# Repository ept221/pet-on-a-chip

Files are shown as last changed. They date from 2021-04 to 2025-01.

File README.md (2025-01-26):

# Pet On A Chip
Pet on a chip is a project which condenses the control logic the robot described in Frank DaCosta's book "How to Build Your Own Working Robot Pet" onto a single FPGA. More details, pictures, and videos can be found on this [blog post](https://ezrasrobots.wordpress.com/2021/07/07/pet-on-a-chip/).

## tinySoC
tinySoC is a small system on a chip responsible for controlling the robot. It consists of an 8-bit CPU, an 80 column VGA graphics controller, a programmable interrupt controller, GPIO, counter/timer peripherals, dual closed loop motor controllers, a servo controller, a sonar controller, and a UART, all implemented on an iCE40 FPGA. It also comes with an assembler and utilities for loading programs into the chip's internal block memory without having to rerun synthesis and place-and-route.

## The CPU
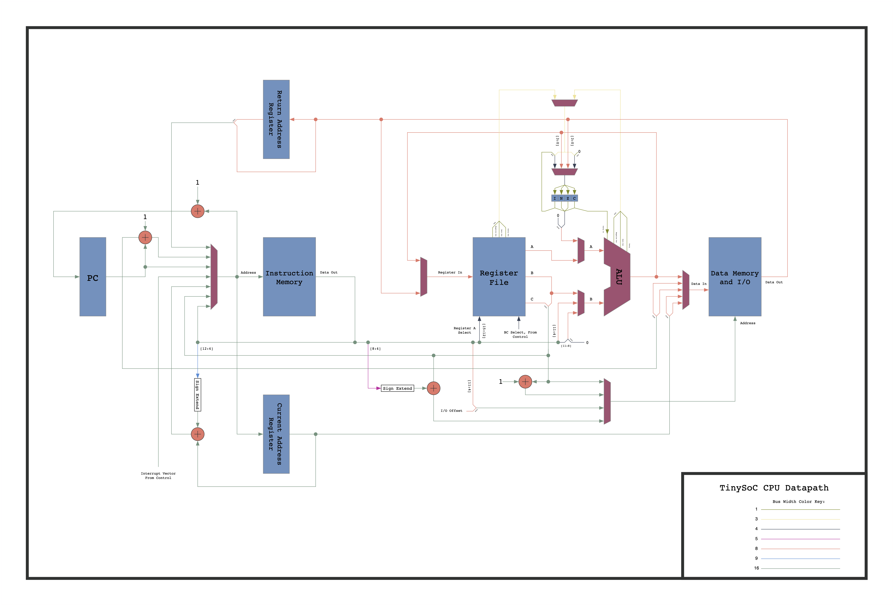
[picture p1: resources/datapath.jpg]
datapath

The CPU is an 8-bit RISC core, with a Harvard architecture. It has a 16-bit wide instruction memory, an 8-bit wide data memory, and both have a 16-bit address. The CPU has 16 general purpose 8-bit registers along with a 4-bit status register. The processor is not fully pipelined, but does fetch the next instruction while executing the current one. Most instructions execute in a single clock cycle, but a few take two or three.

## The GPU
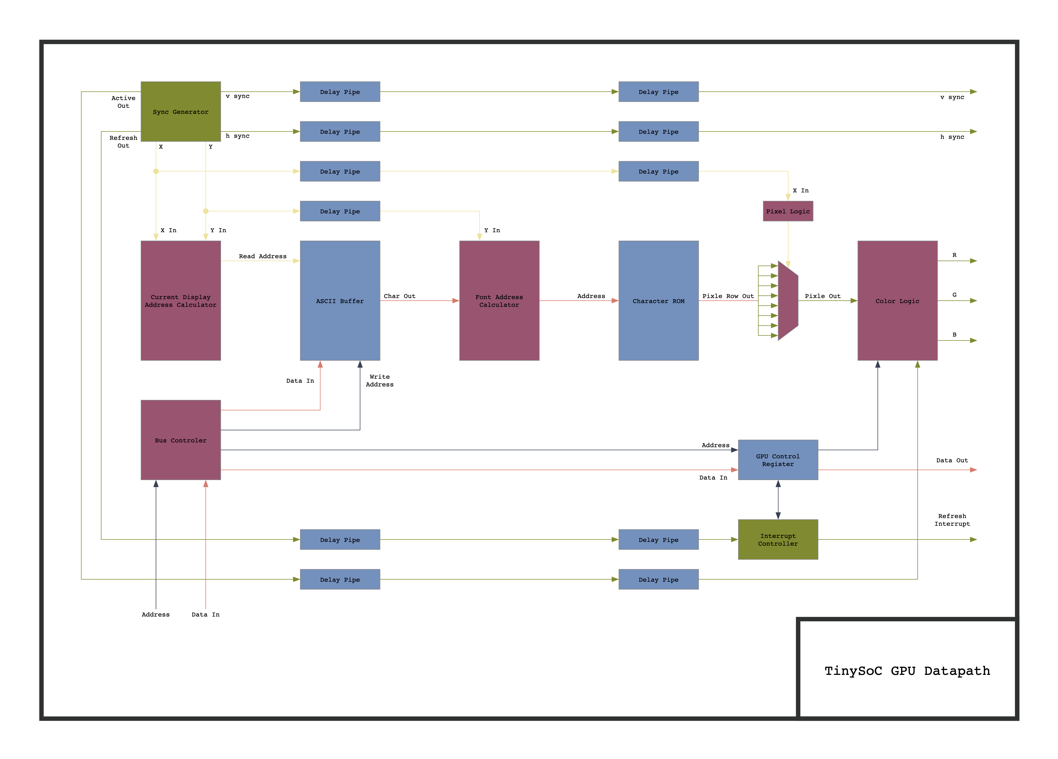
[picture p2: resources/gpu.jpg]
gpu

The GPU operates in a monochrome 80 column text mode, and outputs a VGA signal at a resolution of 640 by 480 at 60 frames per second. The GPU contains an ASCII buffer which the user can write to in order to display messages on the screen. A control register allows the user to set the text to one of 7 colors, and to enable an interrupt to the CPU which fires every time a frame finishes and enters the blanking period. Not shown in the diagram is control logic that allows the screen to be scrolled upwards by writing to the control register.

## The Instruction Set
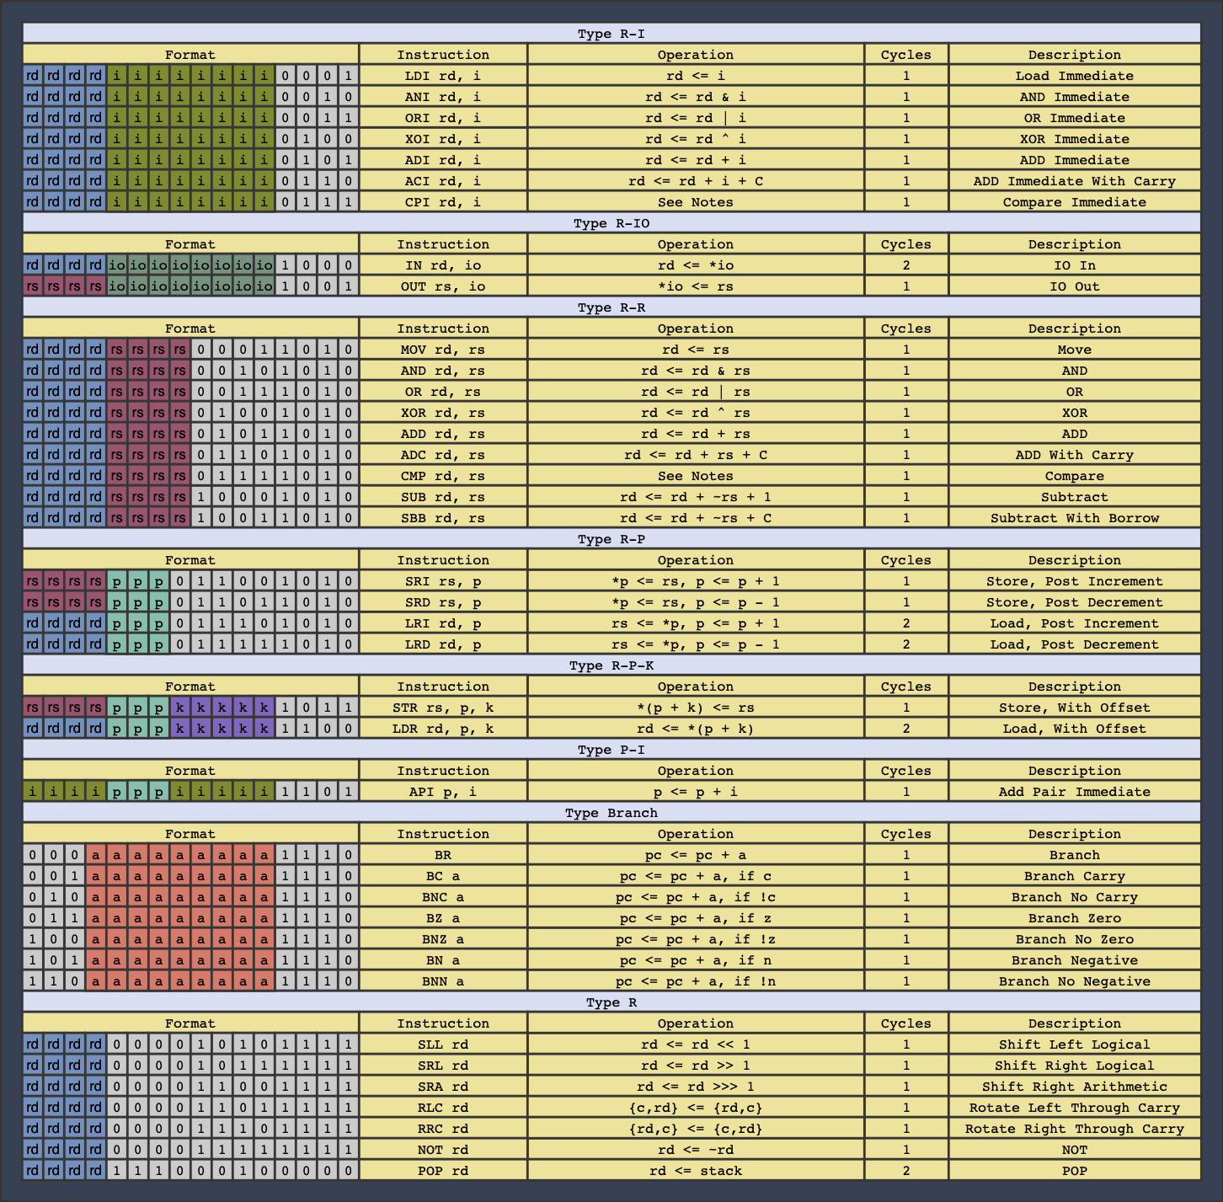
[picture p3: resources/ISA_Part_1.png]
instruction set part 1

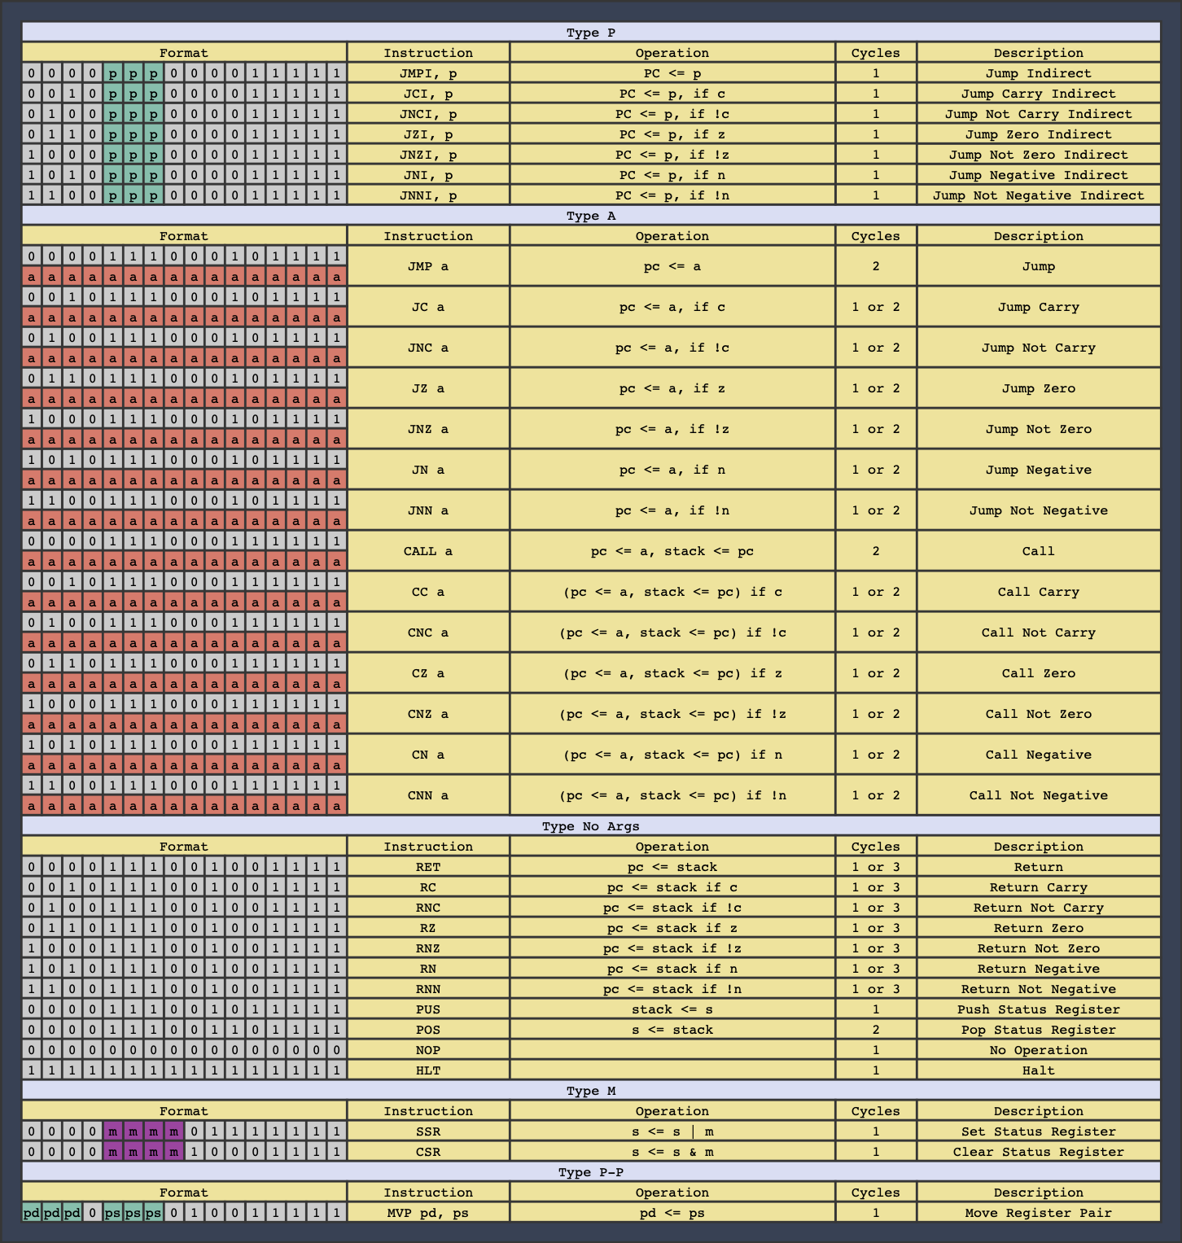
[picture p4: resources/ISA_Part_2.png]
instruction set part 2


## The PCBs
The main board:
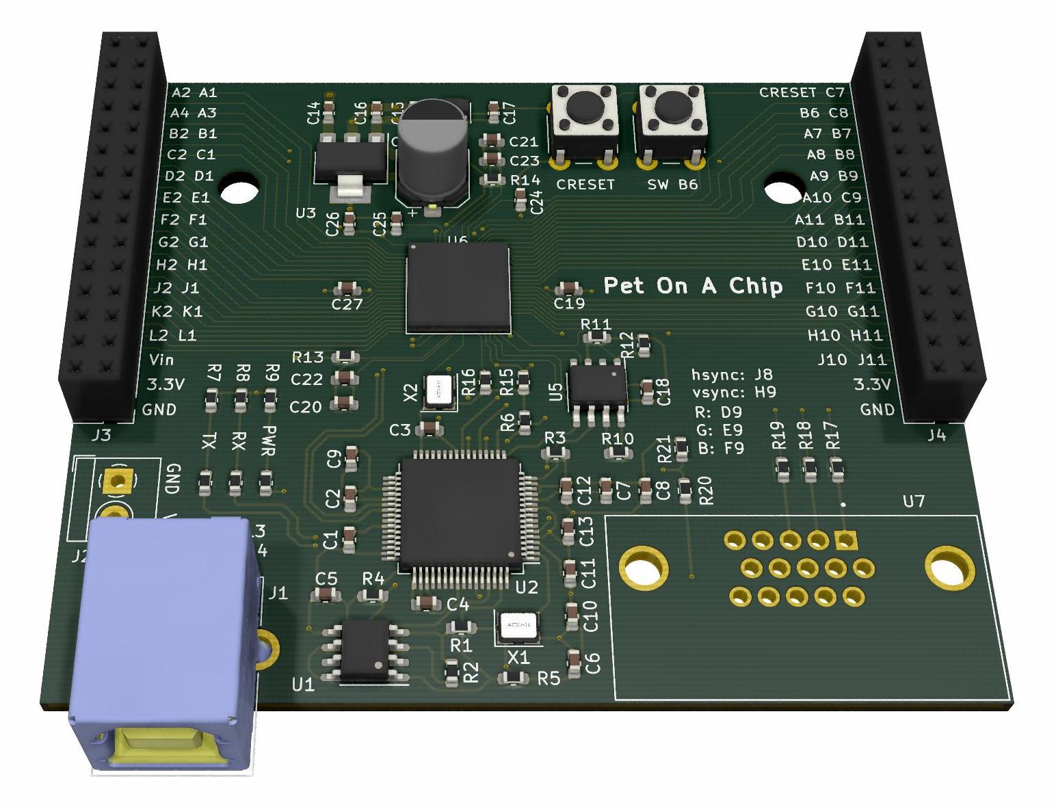
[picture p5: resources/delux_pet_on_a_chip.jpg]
Delux Pet on a Chip

The expantion board:
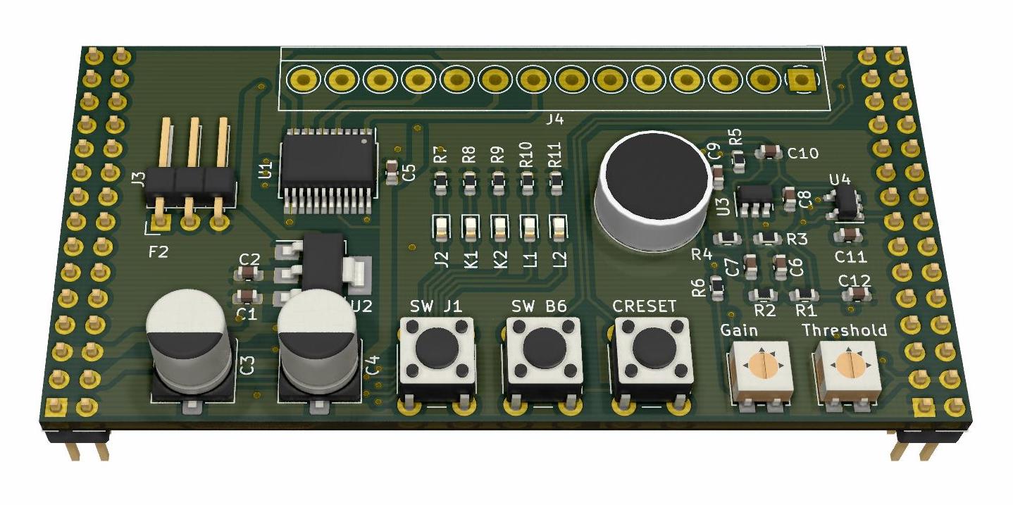
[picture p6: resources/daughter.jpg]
Daughter Board

## The Assembler

The assembler is case insensitive.

### Comments
Comments begin with semicolons.
```assembly
        .code
        ldi r0, 1 ; This is a comment
```

### Constants
Constants are in decimal by default, but hexadecimal and binary are also supported. Constants can also be negative and are stored in two's complement form when assembled. Chars can also be entered as constants.
```assembly
        .code
        ldi r0, 10     ; Decimal constant
        ldi r0, 0x0A   ; Hexadecimal constant
        ldi r0, 0b1010 ; Binary constant
        ldi r0, -10    ; A negative constant
        ldi r0, 'a'    ; A char constant
        ldi r0, '\n'   ; An escaped char constant
```

### Label Definitions
Label definitions may be any string ending with a colon, as long as the string is not in the form of a constant or is one of the reserved keywords

```assembly
        .code
        ldi r0, 10
loop:   adi r0, -1
        bnz loop
        hlt
```

### Directives

#### .code
Specifies that the following lines are code to be assembled and placed in instruction memory.

#### .data
Specifies that the following lines are data to be placed in data memory.

#### .org
Sets the origin to the given address. Only forward movement of the origin is permitted.
```assembly
        .code
        ldi r0, 1
        out r0, 0
        br foo
        
        .org 0x0B
foo:    out r0, 1
        hlt

;*************************************************************************
; Assembles to the following:
; Address        Label          Code                     Source
; ------------------------------------------------------------------------
; 0x0000                        0b0000000000010001       LDI R0, 1        
; 0x0001                        0b0000000000001001       OUT R0, 0        
; 0x0002                        0b0000000010011110       BR FOO           
; 0x000B         FOO:           0b0000000000011001       OUT R0, 1        
; 0x000C                        0b1111111111111111       HLT 
```

#### .db
Writes one or more data bytes sequentially into data memory.
```assembly
        .data
        .db 0x01, 0x44, 0x73

;*************************************************************************
; Assembles to the following:
; Address        Label          Data
; ------------------------------------------
; 0x0000                        0x01
; 0x0001                        0x44
; 0x0002                        0x73
```

#### .ds
Defines a block of space in the data memory. This is useful for allocating room for a buffer.
```assembly
        .data
        .db 5
        .ds 3
        .db 7

;*************************************************************************
; Assembles to the following:
; Address        Label          Data
; ------------------------------------------
; 0x0000                        0x05                                         
; 0x0004                        0x07 
```

#### .string
Writes a null terminated ASCII string into data memory. Double quotes and backslashes must be escaped with a backslash.

```assembly
        .data
        .string "The robot says \"Hi!\""
        
;*************************************************************************
; Assembles to the following:
; Address        Label          Data
; ------------------------------------------
; 0x0000                        0x54
; 0x0001                        0x68
; 0x0002                        0x65
; 0x0003                        0x20
; 0x0004                        0x72
; 0x0005                        0x6F
; 0x0006                        0x62
; 0x0007                        0x6F
; 0x0008                        0x74
; 0x0009                        0x20
; 0x000A                        0x73
; 0x000B                        0x61
; 0x000C                        0x79
; 0x000D                        0x73
; 0x000E                        0x20
; 0x000F                        0x22
; 0x0010                        0x48
; 0x0011                        0x69
; 0x0012                        0x21
; 0x0013                        0x22
; 0x0014                        0x00
```

#### .ostring
Write a ASCII string into data memory. The string is open, which means that it is not null terminated. This is useful if you have a long string that you want to split up into multiple lines in the assembly source file.

```assembly
        .data
        .ostring "Hi! "
        .string  "Bye!"

;*************************************************************************
; Assembles to the following:
; Address        Label          Data
; ------------------------------------------
; 0x0000                        0x48
; 0x0001                        0x69
; 0x0002                        0x21
; 0x0003                        0x20
; 0x0004                        0x42
; 0x0005                        0x79
; 0x0006                        0x65
; 0x0007                        0x21
; 0x0008                        0x00
```

#### .define
Equates a symbol with a number.
```assembly
        .code
        .define foo, 5
        ldi r0, foo
        hlt
        
;*************************************************************************
; Assembles to the following:        
; Address        Label          Code                     Source
; ------------------------------------------------------------------------
; 0x0000                        0b0000000001010001       LDI R0, FOO     
; 0x0001                        0b0000000011110000       HLT  
```

### Expressions
Any time an instruction or directive requires a numerical argument, an expression can be used.
Supported operations inside expressions include addition and subtraction. The location counter $ is also made available. If an instruction is two bytes long then $ refers to the address of the second byte. Expressions may contain symbols, but must resolve within two passes of the assembler, and if used for directive arguments, must resolve in a single pass.

```assembly
; Example resolution in one pass
        .code
        .define foo, 5
        ldi r0, foo + 7
        hlt

;*************************************************************************
; Assembles to the following:
; Address        Label          Code                     Source
; ------------------------------------------------------------------------
; 0x0000                        0b0000000011000001       LDI R0, FOO + 7
; 0x0001                        0b0000000011110000       HLT
```
```assembly
; Example resolution in two passes
        .code
        ldi r0, foo + 7
        hlt
        .define foo, 5

;*************************************************************************
; Assembles to the following:
; Address        Label          Code                     Source
; ------------------------------------------------------------------------
; 0x0000                        0b0000000011000001       LDI R0, FOO + 7
; 0x0001                        0b0000000011110000       HLT
```
```assembly
; Example resolution in two passes with $
        .code
        ldi r0, $
        jmp $ + foo
        .define foo, 2
        nop
        nop
        nop
        hlt

;*************************************************************************
; Assembles to the following:
; Address        Label          Code                     Source
; ------------------------------------------------------------------------
; 0x0000                        0b0000000000000001       LDI R0, $
; 0x0001                        0b0000000010111000       JMP $ + FOO
; 0x0002                        0b0000000000000100
; 0x0003                        0b0000000000000000       NOP
; 0x0004                        0b0000000000000000       NOP
; 0x0005                        0b0000000000000000       NOP
; 0x0006                        0b0000000011110000       HLT
```
## The Development Process
To perform synthesis and place-and-route, run:
```bash
make synth
make pnr
```
To assemble a demo program, run:
```bash
./assemble programs/shell.asm shell
```
To upload the configuration bitstream for the previously assembled program, run:
```bash
./upload shell
```
You will now be able to interact with a basic shell over the UART at 115200 baud. Additionally, the output will also be sent over the VGA interface.

## Requirements
- Yosys for synthisis
- nextpnr for place and route
- icestorm tools for icebram and iceprog

## Peripherals

There are a variety of memory mapped peripherals included in the system. The memory map is configured in `soc/src/d_ram_and_io/d_ram_and_io.v`. Currently addresses `0x0000` to `0x07FF` are mapped to data ram. The peripherals are mapped from `0x1000` to `0x10FF`. The instructions `in` and `out` are designed to allow for quickly and easily reading and writing to peripherals within this address range. For example, `out r1, 5` writes the value in r1 to address `0x1005`. In contrast, when reading and writing to data memory, or writing to the graphics buffer which is from `0x2000` to `0x2960`, `in` and `out` cannot be used, and the other load and store instructions must be used instead, which require setting up a pointer in a register pair to the memory location you want to operate on.

### GPIO
|Address|Register|r/w|Description|
|---|---|---|---|
|0x1000|Direction|r/w|Sets GPIO pins to input or output|
|0x1001|Port|r/w|Write values to be outputed|
|0x1002|Pin|r|Read values on pins|

### Counter Timer
|Address|Register|r/w|Description|
|---|---|---|---|
|0x1003| Scale LSB|r/w||
|0x1004| Scale MSB|r/w||
|0x1005| Control|r/w||
|0x1006| CMPR0|r/w||
|0x1007| CMPR1|r/w||
|0x1008| Counter|r||

### UART
|Address|Register|r/w|Description|
|---|---|---|---|
|0x1009| Baud|r/w| Configures the baudrate|
|0x100A| Status|r| Signals empty tx buffer and or full rx buffer|
|0x100B| Buffer |r/w| Write to tx buffer, read from rx buffer|

### Motor Controller
|Address|Register|r/w|Description|
|---|---|---|---|
|0x100C| Control |r/w| Sets the motors' directions|
|0x100D| Enable  |r/w| Enables the motor driver|
|0x100E| Speed 0 |r/w| Target speed of motor 0|
|0x100F| Speed 1 |r/w| Target speed of motor 1|
|0x1010| RPM 0 |r| Actual speed of motor 0|
|0x1011| RPM 1 |r| Actual speed of motor 1|

### Servo Controller
|Address|Register|r/w|Description|
|---|---|---|---|
|0x1012| Position|r/w| Sets the position of the servo|

### Sonar Controller
|Address|Register|r/w|Description|
|---|---|---|---|
|0x1013| Status | r| Signals new reading in range register |
|0x1014| Range | r| Holds the measured distance|

### Programmable Interrupt Controller
|Address|Register|r/w|Description|
|---|---|---|---|
|0x1015| Vect 0 Low|r/w| LSBs of interrupt vector 0|
|0x1016| Vect 0 High|r/w| MSBs of interrupt vector 0|
|0x1017| Vect 1 Low|r/w| LSBs of interrupt vector 1|
|0x1018| Vect 1 High|r/w| MSBs of interrupt vector 1|
|0x1019| Vect 2 Low|r/w| LSBs of interrupt vector 2|
|0x101A| Vect 2 High|r/w| MSBs of interrupt vector 2|
|0x101B| Vect 3 Low|r/w| LSBs of interrupt vector 3|
|0x101C| Vect 3 High|r/w| MSBs of interrupt vector 3|

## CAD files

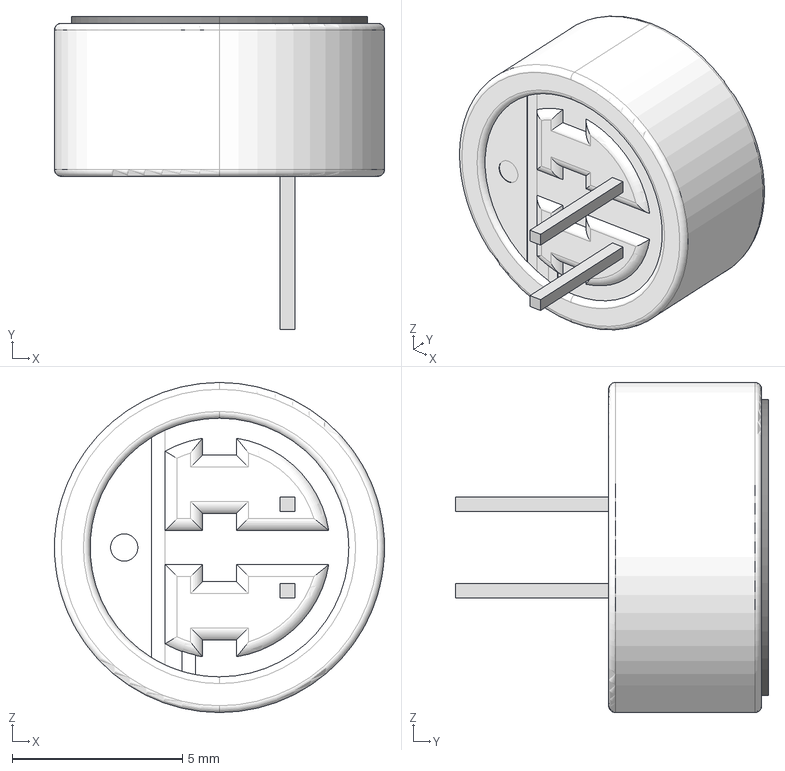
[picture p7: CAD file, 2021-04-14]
pcb/daughter/3D/cma-4544pf-w.stp
9.70 x 9.20 x 9.70 mm

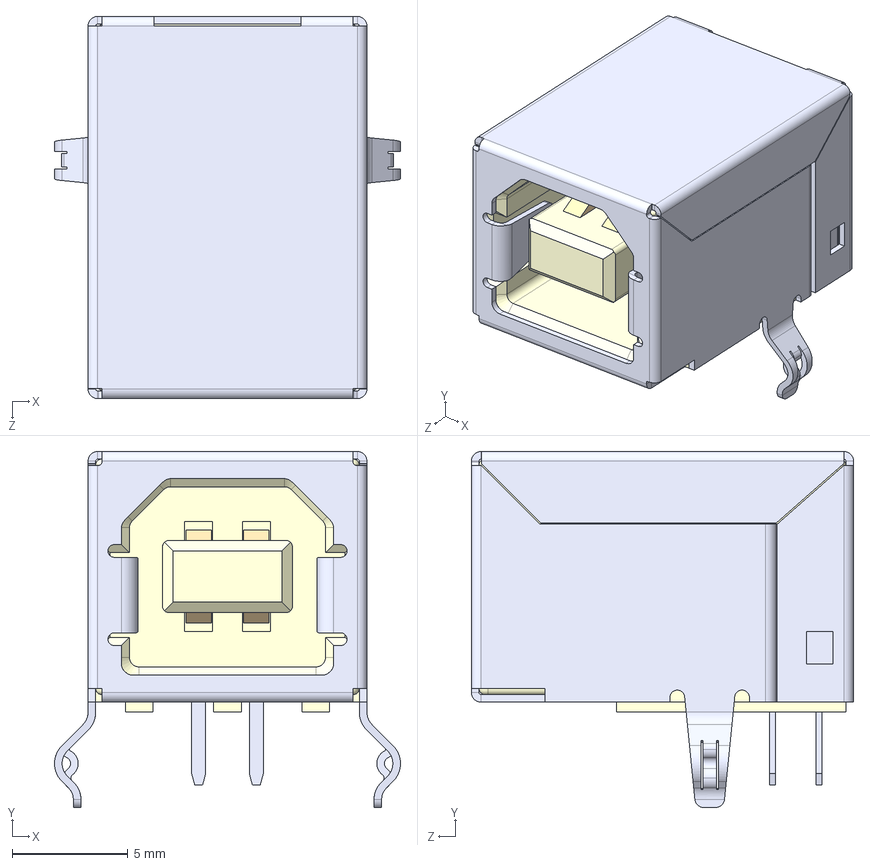
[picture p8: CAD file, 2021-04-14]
pcb/pet on a chip/3D/USB.STEP
14.9 x 15.4 x 16.5 mm

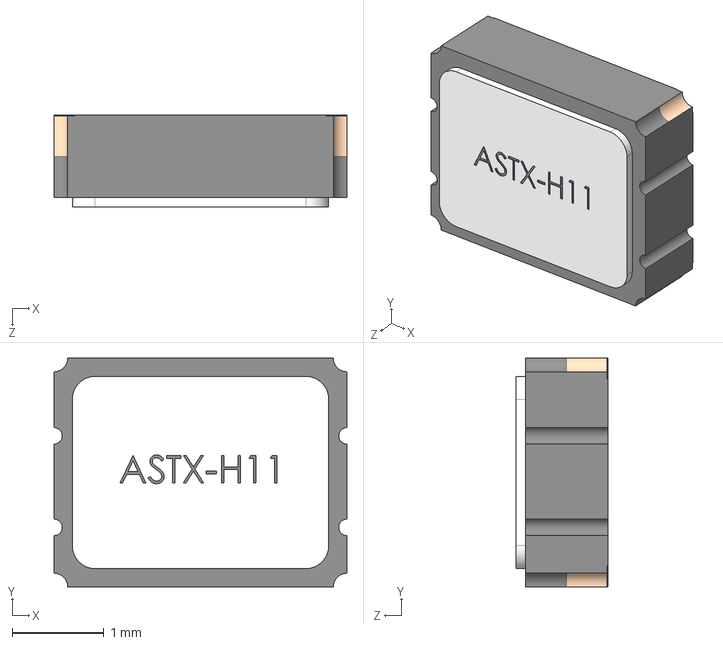
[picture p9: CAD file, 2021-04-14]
pcb/pet on a chip/3D/ASTX-H11.STEP
3.20 x 2.50 x 1.00 mm

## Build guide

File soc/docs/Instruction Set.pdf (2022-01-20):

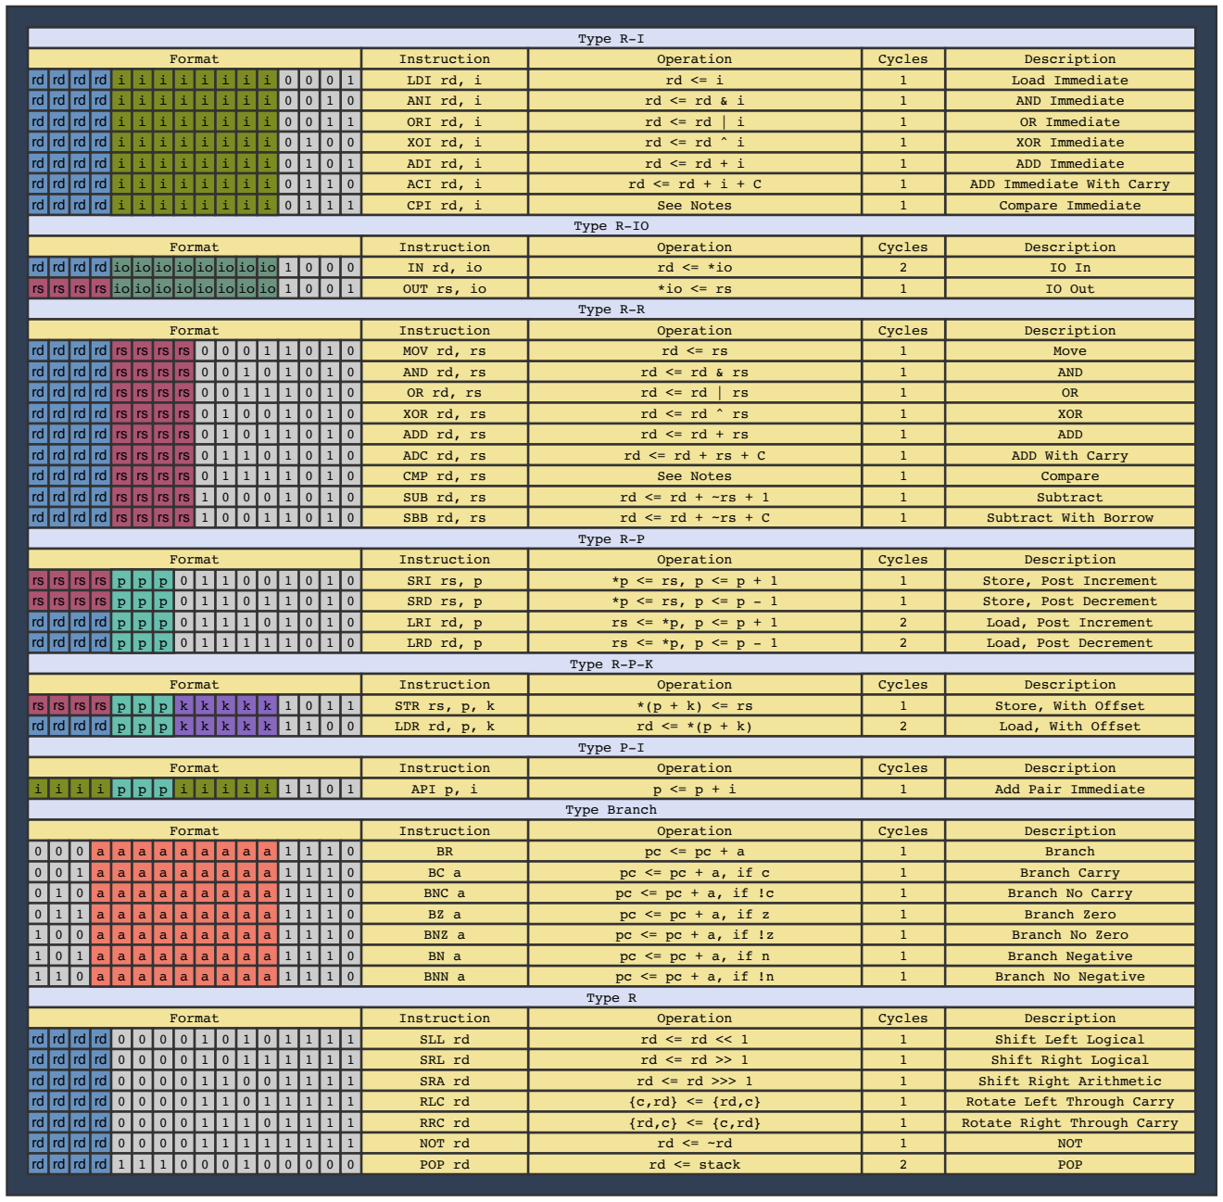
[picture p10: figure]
Type R-I; Format; Instruction; Operation; Cycles; Description; LDI rd, i; ANI rd, i; XOI rd, i; ADI rd, i ACI rd, i; CPI rd, i; ORI rd, i; Load Immediate; AND Immediate; OR Immediate; XOR Immediate; ADD Immediate ADD Immediate With Carry; Compare Immediate; See Notes; Type R-IO; OUT rs, io; IO Out; Cycles 1; Type R-R; AND rd, rs; XOR rd, rs; ADD rd, rs; ADC rd, rs; CMP rd, rs; SUB rd, rs; SBB rd, rs; MOV rd, rs; Cycles 111111111; AND; XOR; ADD; ADD With Carry; Compare; Subtract; Subtract With Borrow; Move; Type R-P; SRI rs, p; LRI rd, p; SRD rs, p; LRD rd, p; Store, Post Increment; Store, Post Decrement; Load, Post Increment; Load, Post Decrement; Type R-P-K; STR rs, p, k; LDR rd, p, k; Store, With Offset; Load, With Offset; Type P-I; API p, i; Add Pair Immediate; Type Branch; BNC a; BNZ a; BNN a; Branch; Branch Carry; Branch No Carry; Branch No Zero; Branch No Negative; Branch Zero; Branch Negative; Type R; SLL rd; SRL rd; SRA rd; RLC rd; RRC rd; NOT rd; Shift Left Logical; Shift Right Logical; Shift Right Arithmetic; Rotate Left Through Carry; Rotate Right Through Carry; NOT; POP rd; rd <= stack; POP
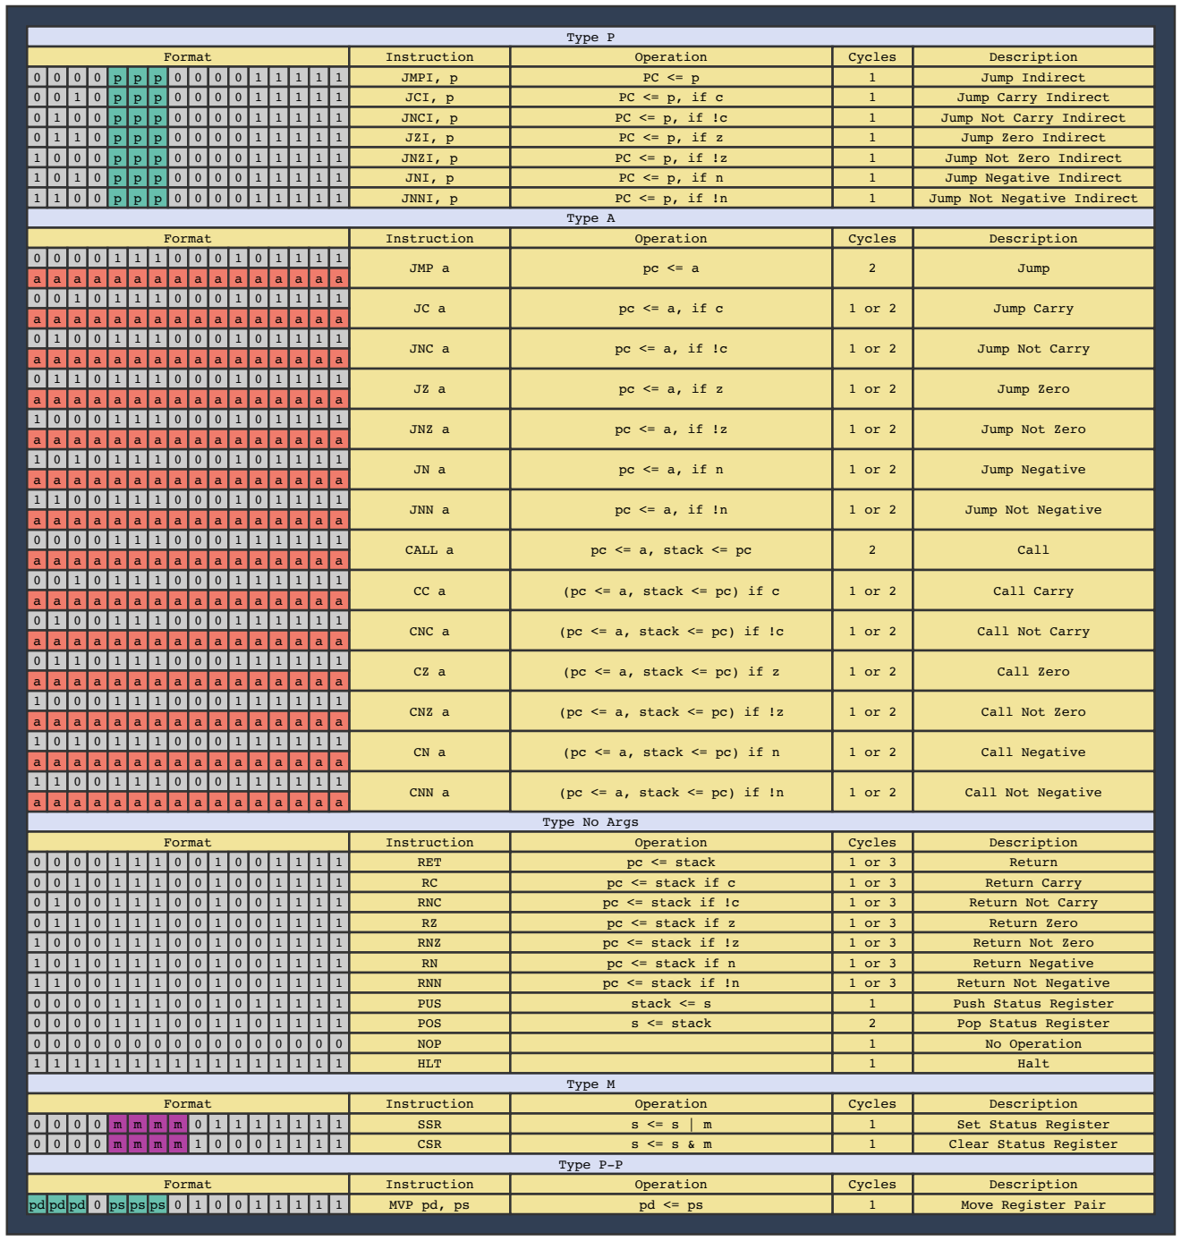
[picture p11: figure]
Type A; Format; Instruction; Operation; Description; JMP a; JNC a; JNZ a; JNN a; CALL a; CNC a; CNZ a; CNN a; Type No Args; pc <= a, stack <= pc; (pc <= a, stack <= pc) if c; (pc <= a, stack <= pc) if !c; (pc <= a, stack <= pc) if z; (pc <= a, stack <= pc) if !z; (pc <= a, stack <= pc) if n; (pc <= a, stack <= pc) if !n; Jump; Jump Carry; Jump Not Carry; Cycles 2; Jump Zero; Jump Not Zero; Jump Negative; Jump Not Negative; Call; Call Carry; Call Not Carry; Call Zero; Call Not Zero; Call Negative; Call Not Negative; Type P; Cycles; JMPI, p; JCI, p; JNCI, p; JZI, p; JNZI, p JNI, p; JNNI, p; Jump Indirect; Jump Carry Indirect; Jump Not Carry Indirect; Jump Not Negative Indirect; Jump Negative Indirect; Jump Not Zero Indirect; Jump Zero Indirect; RET; RNC; RNZ; RNN; pc <= stack; pc <= stack if c; pc <= stack if !c; pc <= stack if z; pc <= stack if !z; pc <= stack if n; pc <= stack if !n; Return; Return Carry; Return Not Carry; Return Zero; Return Not Zero; Return Negative; Return Not Negative; PUS; POS; stack <= s; s <= stack; Push Status Register; Pop Status Register; NOP; HLT; No Operation; Halt; Type M; SSR; CSR; Set Status Register; Clear Status Register; Type P-P; MVP pd, ps; Move Register Pair

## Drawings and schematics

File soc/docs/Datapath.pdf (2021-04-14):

# Memory Return Address

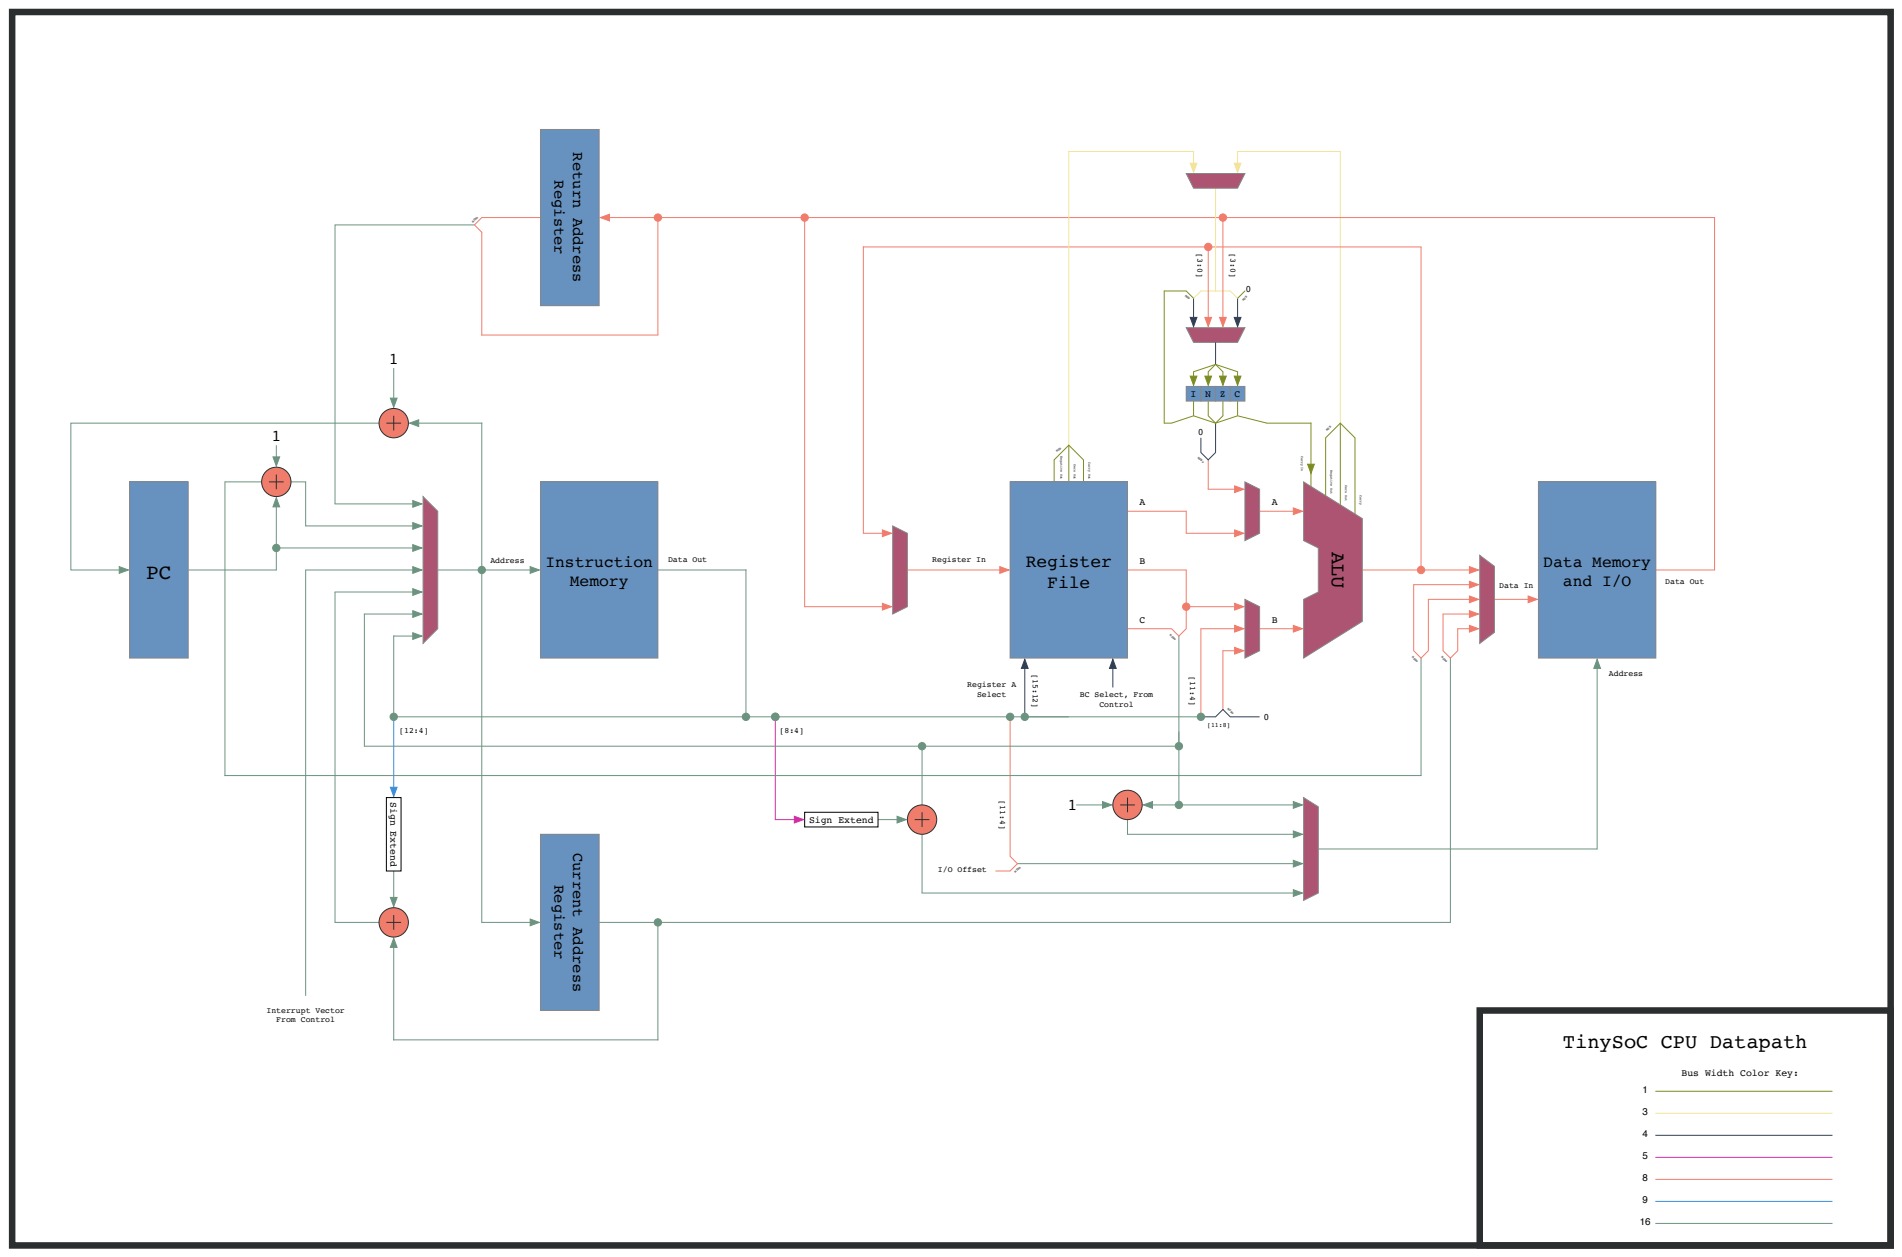
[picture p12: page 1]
Data Out; Register In; MSBs; I/O Offset; Interrupt Vector From Control; MSB; Address; Data In; Carry In; Carry; Zero Out; Negative Out; Instruction; Register; Current Address; Register File; Data Memory and I/O; ALU; Register A Select; Sign Extend; Carry Out

BC Select, From
Control

TinySoC CPU Datapath

Bus Width Color Key:

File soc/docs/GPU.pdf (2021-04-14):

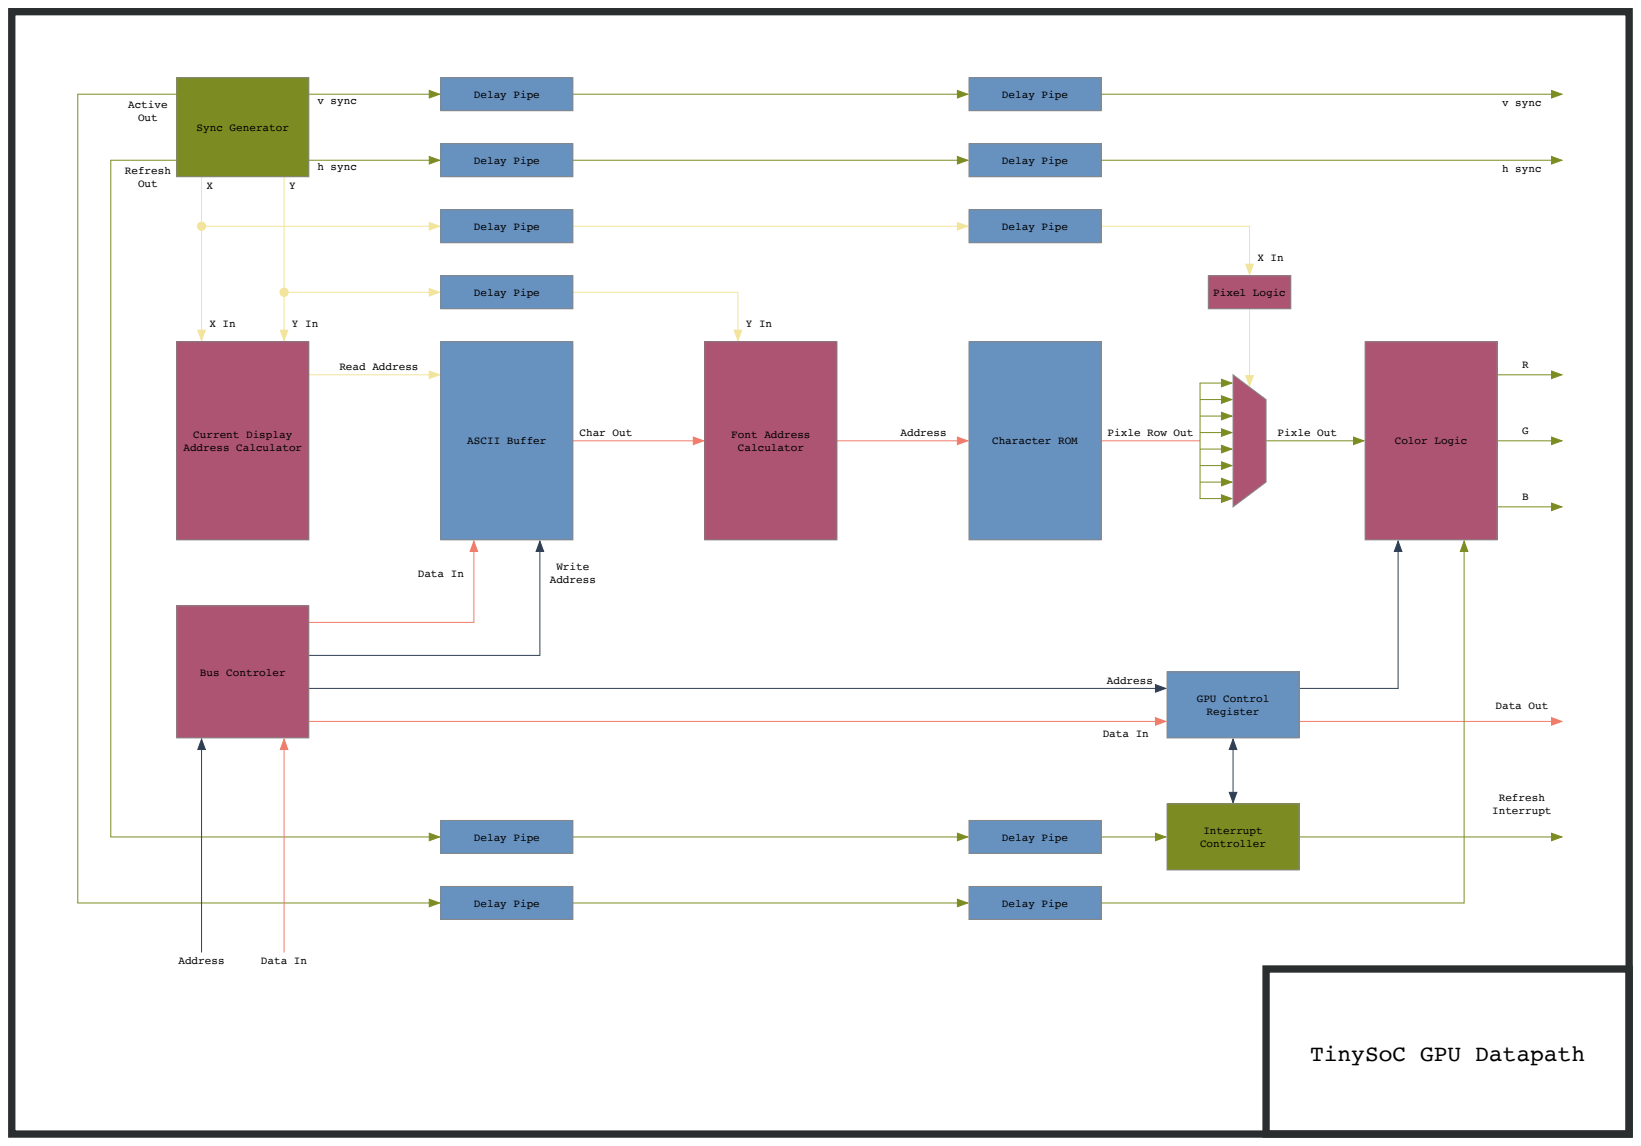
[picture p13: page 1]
Sync Generator; Address Calculator; Character ROM; Read Address; Font Address Calculator; Delay Pipe; h sync; Color Logic; Pixel Logic; v sync; Char Out; Address; Pixle Row Out; Pixle Out; GPU Control Register; Bus Controler; Write; Interrupt Controller; Refresh Interrupt; Data Out; Data In; Refresh Out; Active Out

Delay Pipe v sync

ASCII Buffer Current Display

Address Data In

TinySoC GPU Datapath

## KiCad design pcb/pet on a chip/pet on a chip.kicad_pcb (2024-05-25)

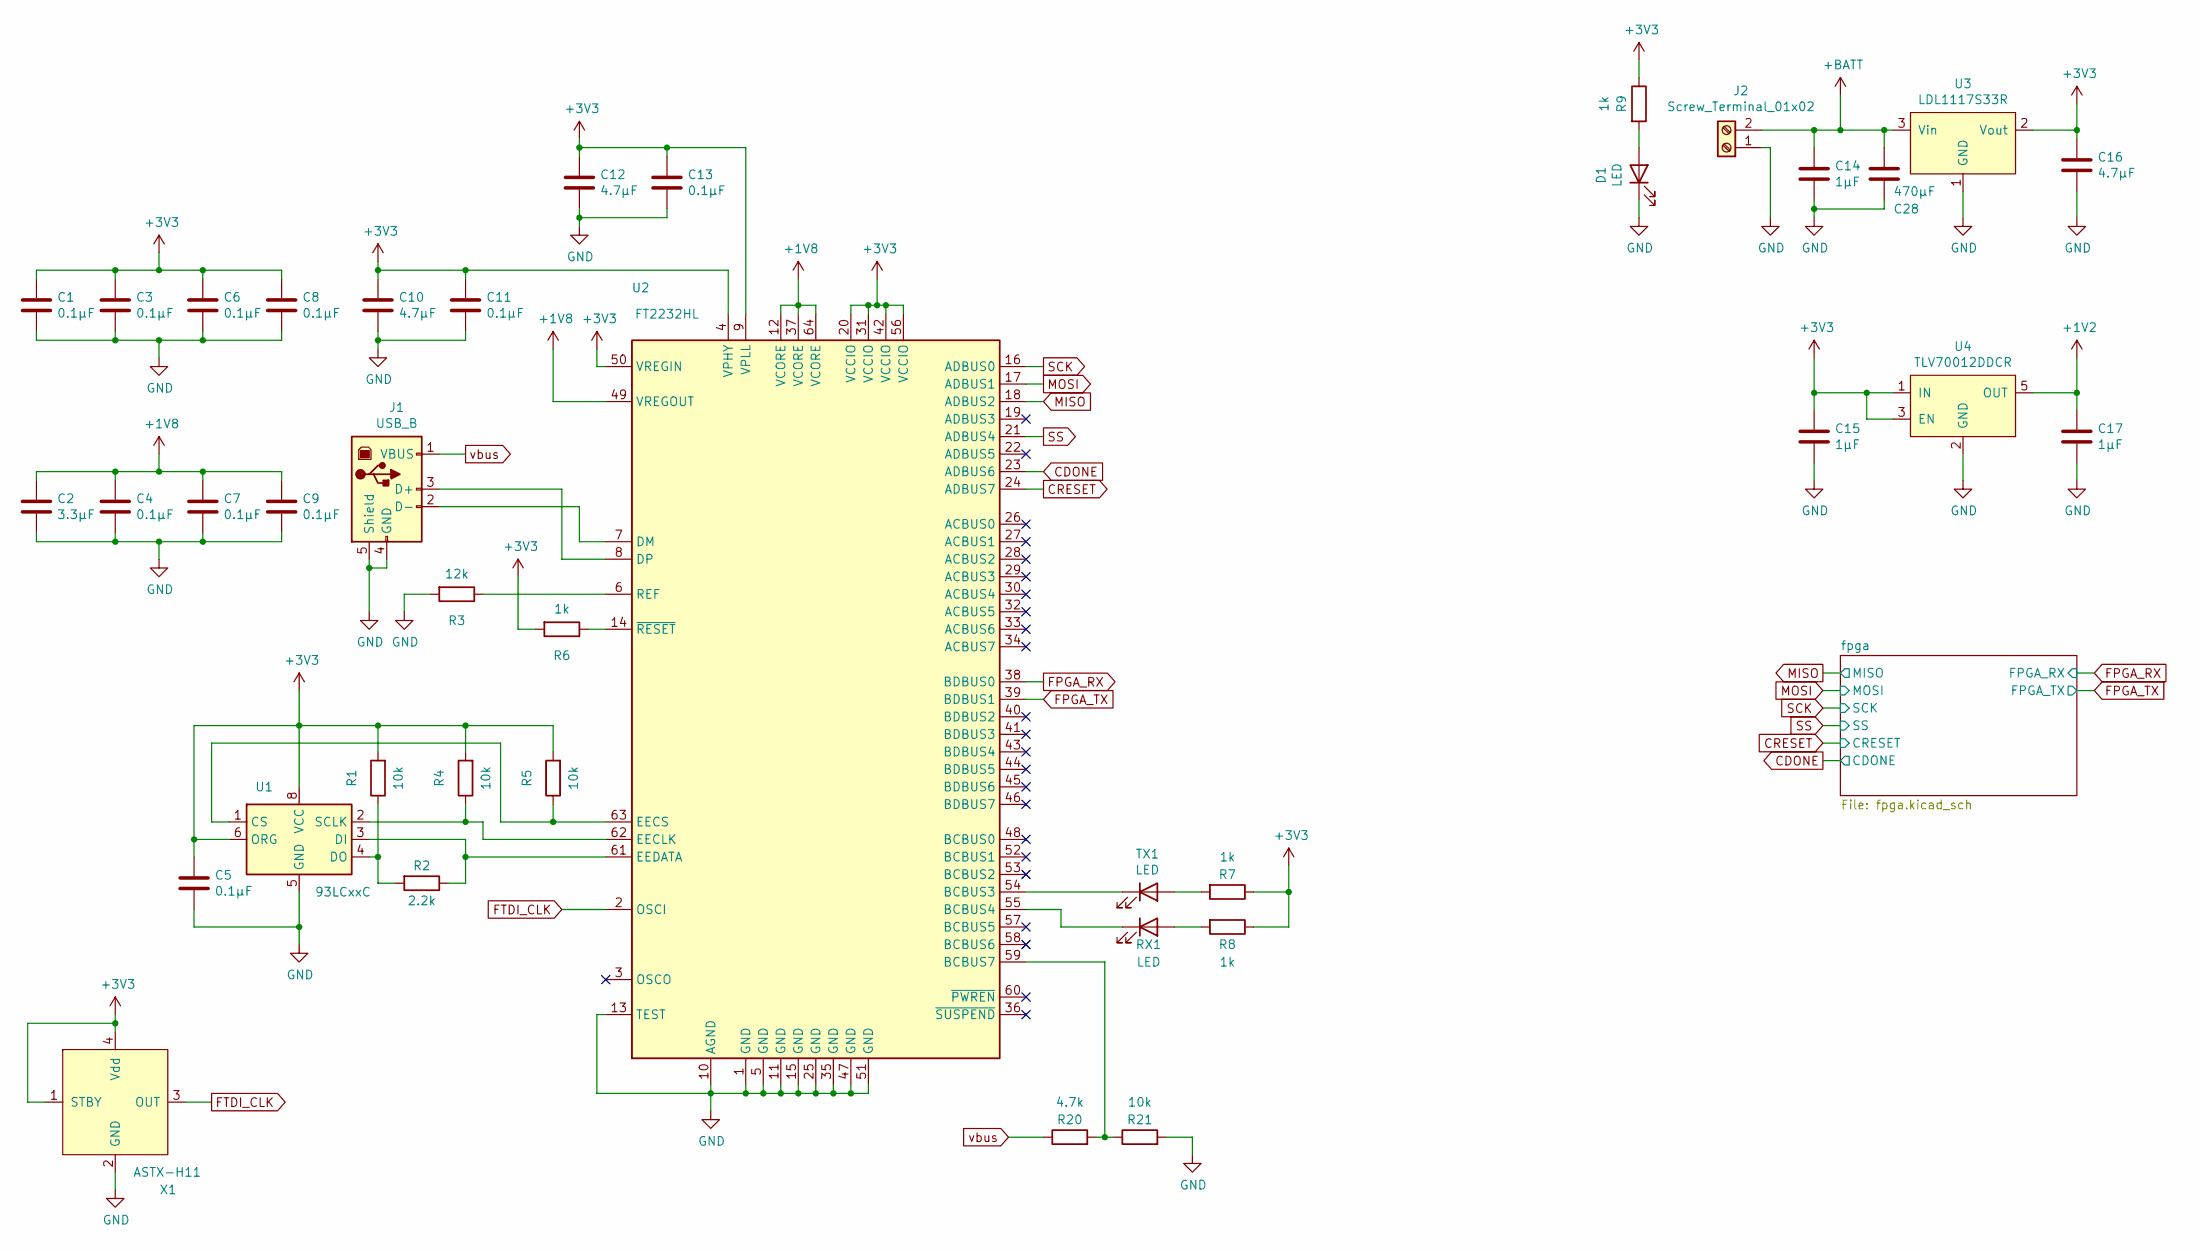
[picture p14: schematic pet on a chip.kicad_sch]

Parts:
C1, C3, C4, C5, C6, C7, C8, C9, C11, C13: 0.1µF; C_0603_1608Metric
C2: 3.3µF; C_0603_1608Metric
C10, C12, C16: 4.7µF; C_0603_1608Metric
C14, C15, C17: 1µF; C_0603_1608Metric
C28: 470µF; CP_Elec_6.3x7.7
D1: LED; R_0603_1608Metric
J1: USB_B; USB_B_OST_USB-B1HSxx_Horizontal
J2: Screw_Terminal_01x02; TerminalBlock_4Ucon_1x02_P3.50mm_Horizontal
R1, R4, R5, R21: 10k; R_0603_1608Metric
R2: 2.2k; R_0603_1608Metric
R3: 12k; R_0603_1608Metric
R6, R7, R8, R9: 1k; R_0603_1608Metric
R20: 4.7k; R_0603_1608Metric
RX1: LED; R_0603_1608Metric
TX1: LED; R_0603_1608Metric
U1: 93LCxxC; SOIC-8_3.9x4.9mm_P1.27mm
U2: FT2232HL; LQFP-64_10x10mm_P0.5mm
U3: LDL1117S33R; SOT-223-3_TabPin2
U4: TLV70012DDCR; SOT-23-5
X1: ASTX-H11; Oscillator_SMD_Abracon_ASE-4Pin_3.2x2.5mm

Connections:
+1V2: C17.1, U4.5 (OUT); also elsewhere on the board
+1V8: C2.1, C4.1, C7.1, C9.1, U2.12 (VCORE), U2.37 (VCORE), U2.49 (VREGOUT), U2.64 (VCORE)
+3V3: C1.1, C3.1, C5.1, C6.1, C8.1, C10.1, C11.1, C12.1, C13.1, C15.1, C16.1, R1.2, R4.2, R5.2, R6.2, R7.1, R8.1, R9.1, U1.6 (ORG), U1.8 (VCC), U2.4 (VPHY), U2.9 (VPLL), U2.20 (VCCIO), U2.31 (VCCIO), U2.42 (VCCIO), U2.50 (VREGIN), U2.56 (VCCIO), U3.2 (Vout), U4.1 (IN), U4.3 (EN), X1.1 (STBY), X1.4 (Vdd); also elsewhere on the board
+BATT: C14.1, C28.1, J2.2, U3.3 (Vin); also elsewhere on the board
CDONE: U2.23 (ADBUS6); also elsewhere on the board
CRESET: U2.24 (ADBUS7); also elsewhere on the board
FPGA_RX: U2.38 (BDBUS0); also elsewhere on the board
FPGA_TX: U2.39 (BDBUS1); also elsewhere on the board
FTDI_CLK: U2.2 (OSCI), X1.3 (OUT)
GND: C1.2, C2.2, C3.2, C4.2, C5.2, C6.2, C7.2, C8.2, C9.2, C10.2, C11.2, C12.2, C13.2, C14.2, C15.2, C16.2, C17.2, C28.2, D1.1 (K), J1.4 (GND), J1.5 (Shield), J2.1, R3.2, R21.2, U1.5 (GND), U2.1 (GND), U2.5 (GND), U2.10 (AGND), U2.11 (GND), U2.13 (TEST), U2.15 (GND), U2.25 (GND), U2.35 (GND), U2.47 (GND), U2.51 (GND), U3.1 (GND), U4.2 (GND), X1.2 (GND); also elsewhere on the board
MISO: U2.18 (ADBUS2); also elsewhere on the board
MOSI: U2.17 (ADBUS1); also elsewhere on the board
unnamed: D1.2 (A), R9.2
unnamed: J1.2 (D-), U2.7 (DM)
unnamed: J1.3 (D+), U2.8 (DP)
unnamed: R1.1, R2.2, U1.4 (DO)
unnamed: R2.1, U1.3 (DI), U2.61 (EEDATA)
unnamed: R3.1, U2.6 (REF)
unnamed: R4.1, U1.2 (SCLK), U2.62 (EECLK)
unnamed: R5.1, U1.1 (CS), U2.63 (EECS)
unnamed: R6.1, U2.14 (~RESET)
unnamed: R7.2, TX1.2 (A)
unnamed: R8.2, RX1.2 (A)
unnamed: R20.2, R21.1, U2.59 (BCBUS7)
unnamed: RX1.1 (K), U2.55 (BCBUS4)
unnamed: TX1.1 (K), U2.54 (BCBUS3)
SCK: U2.16 (ADBUS0); also elsewhere on the board
SS: U2.21 (ADBUS4); also elsewhere on the board
vbus: J1.1 (VBUS), R20.1

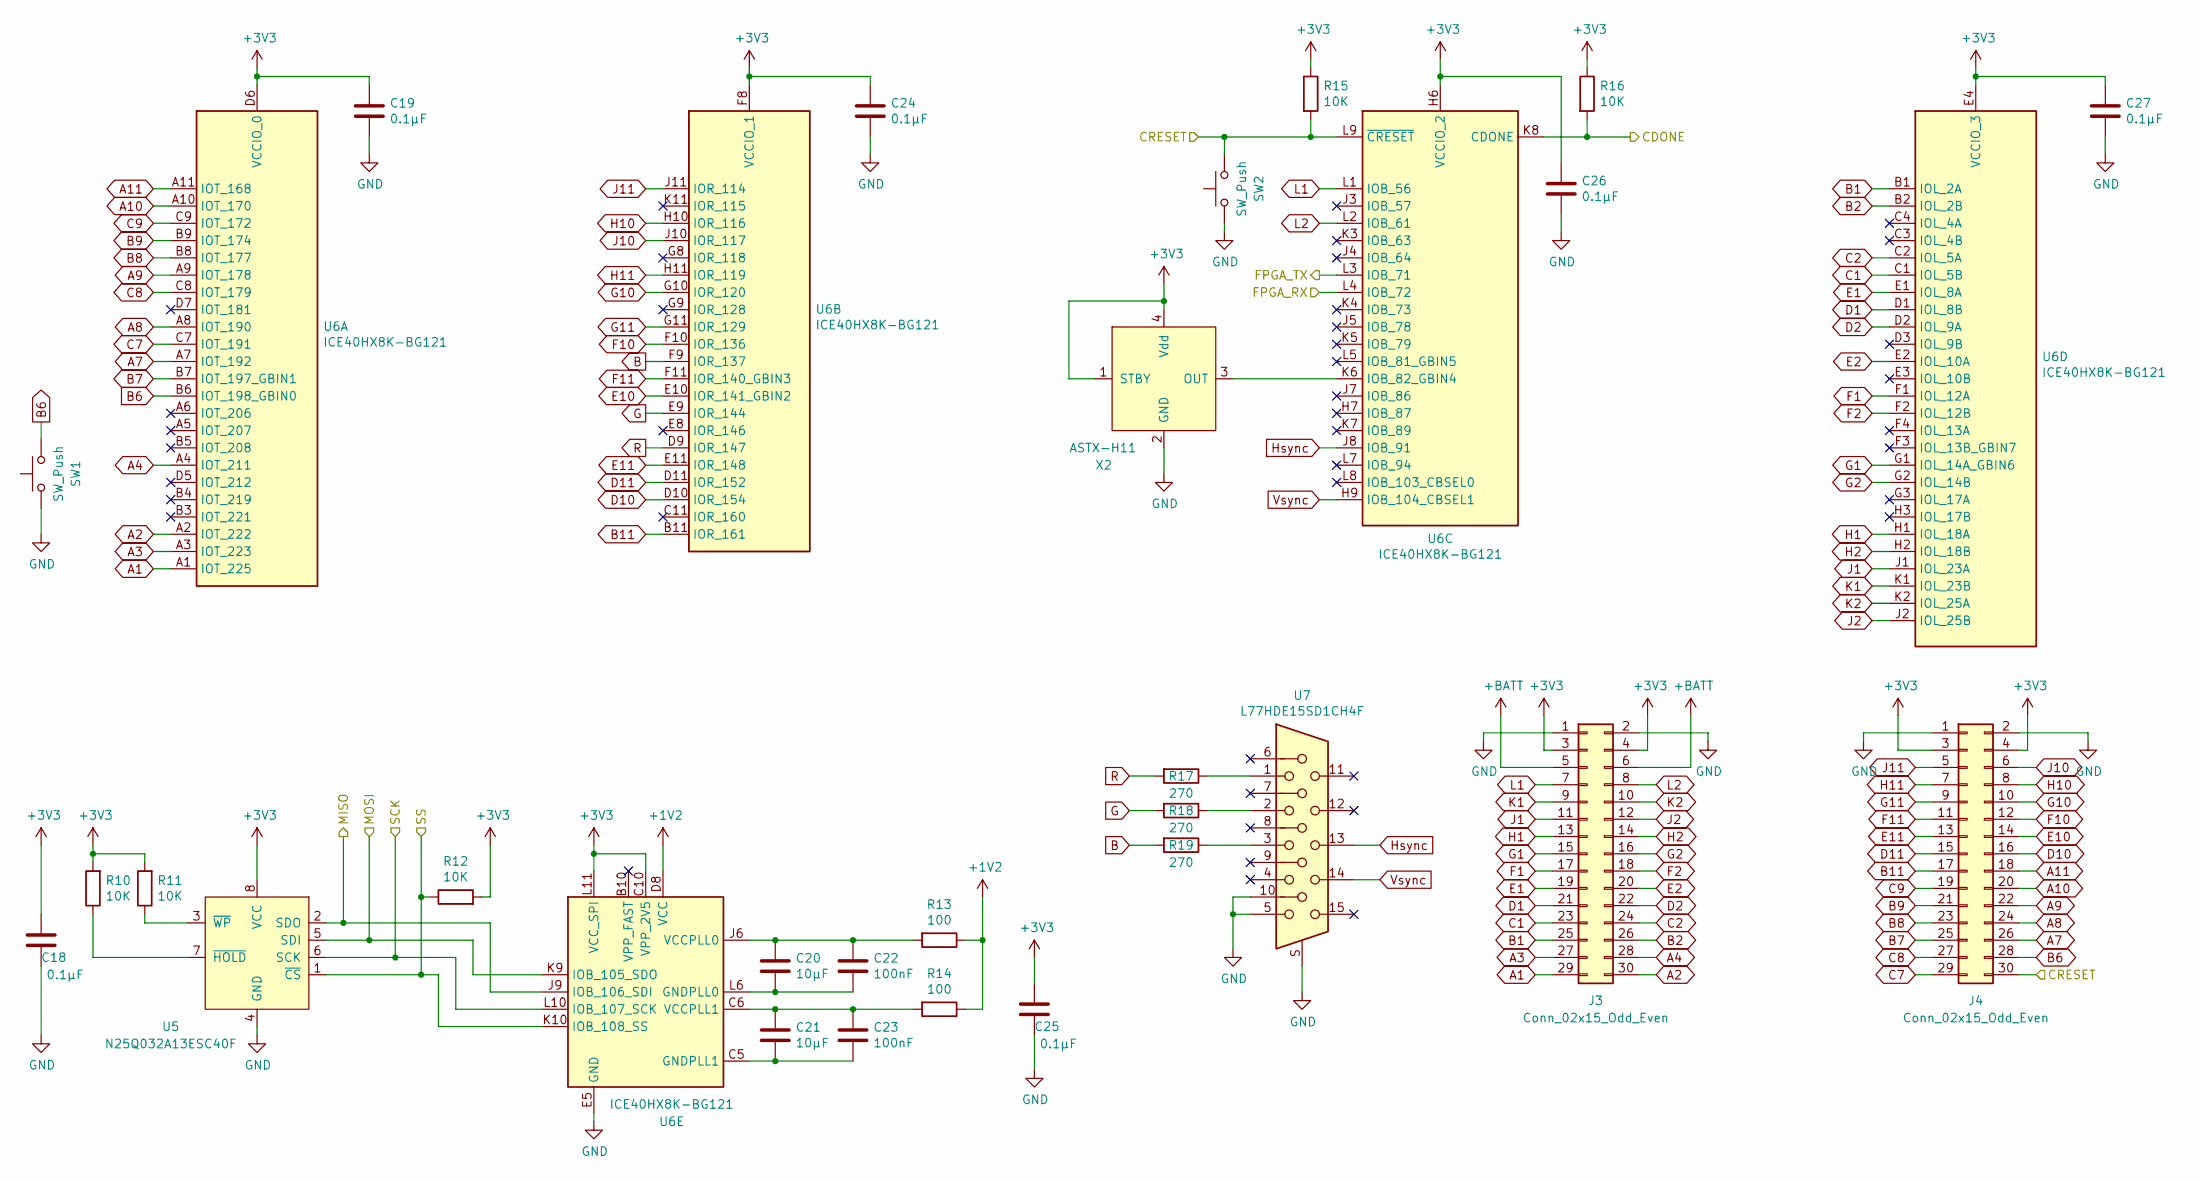
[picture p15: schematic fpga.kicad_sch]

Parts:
C18, C19, C24, C25, C26, C27: 0.1µF; C_0603_1608Metric
C20, C21: 10µF; C_0603_1608Metric
C22, C23: 100nF; C_0603_1608Metric
J3, J4: Conn_02x15_Odd_Even; PinHeader_2x15_P2.54mm_Vertical
R10, R11, R12, R15, R16: 10K; R_0603_1608Metric
R13, R14: 100; R_0603_1608Metric
R17, R18, R19: 270; R_0603_1608Metric
SW1, SW2: SW_Push; SW_PUSH_6mm
U5: N25Q032A13ESC40F; SOP-8_3.9x4.9mm_P1.27mm
U6: ICE40HX8K-BG121; BGA-121_9.0x9.0mm_Layout11x11_P0.8mm_Ball0.4mm_Pad0.35mm_NS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
U7: L77HDE15SD1CH4F; AMPHENOL_L77HDE15SD1CH4F
X2: ASTX-H11; Oscillator_SMD_Abracon_ASE-4Pin_3.2x2.5mm

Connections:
+1V2: R13.1, R14.1, U6.D4 (VCC), U6.D8 (VCC), U6.H4 (VCC), U6.H8 (VCC); also elsewhere on the board
+3V3: C18.2, C19.1, C24.1, C25.2, C26.1, C27.1, J3.3, J3.4, J4.3, J4.4, R10.2, R11.2, R12.2, R15.1, R16.1, U5.8 (VCC), U6.C10 (VPP_2V5), U6.D6 (VCCIO_0), U6.E4 (VCCIO_3), U6.F8 (VCCIO_1), U6.G4 (VCCIO_3), U6.H6 (VCCIO_2), U6.L11 (VCC_SPI), X2.1 (STBY), X2.4 (Vdd); also elsewhere on the board
+BATT: J3.5, J3.6; also elsewhere on the board
A1: J3.29, U6.A1 (IOT_225)
A2: J3.30, U6.A2 (IOT_222)
A3: J3.27, U6.A3 (IOT_223)
A4: J3.28, U6.A4 (IOT_211)
A7: J4.26, U6.A7 (IOT_192)
A8: J4.24, U6.A8 (IOT_190)
A9: J4.22, U6.A9 (IOT_178)
A10: J4.20, U6.A10 (IOT_170)
A11: J4.18, U6.A11 (IOT_168)
B: R19.2, U6.F9 (IOR_137)
B1: J3.25, U6.B1 (IOL_2A)
B2: J3.26, U6.B2 (IOL_2B)
B6: J4.28, SW1.2, U6.B6 (IOT_198_GBIN0)
B7: J4.25, U6.B7 (IOT_197_GBIN1)
B8: J4.23, U6.B8 (IOT_177)
B9: J4.21, U6.B9 (IOT_174)
B11: J4.17, U6.B11 (IOR_161)
C1: J3.23, U6.C1 (IOL_5B)
C2: J3.24, U6.C2 (IOL_5A)
C7: J4.29, U6.C7 (IOT_191)
C8: J4.27, U6.C8 (IOT_179)
C9: J4.19, U6.C9 (IOT_172)
CDONE: R16.2, U6.K8 (CDONE); also elsewhere on the board
CRESET: J4.30, R15.2, SW2.2, U6.L9 (~CRESET); also elsewhere on the board
D1: J3.21, U6.D1 (IOL_8B)
D2: J3.22, U6.D2 (IOL_9A)
D10: J4.16, U6.D10 (IOR_154)
D11: J4.15, U6.D11 (IOR_152)
E1: J3.19, U6.E1 (IOL_8A)
E2: J3.20, U6.E2 (IOL_10A)
E10: J4.14, U6.E10 (IOR_141_GBIN2)
E11: J4.13, U6.E11 (IOR_148)
F1: J3.17, U6.F1 (IOL_12A)
F2: J3.18, U6.F2 (IOL_12B)
F10: J4.12, U6.F10 (IOR_136)
F11: J4.11, U6.F11 (IOR_140_GBIN3)
FPGA_RX: U6.L4 (IOB_72); also elsewhere on the board
FPGA_TX: U6.L3 (IOB_71); also elsewhere on the board
G: R18.2, U6.E9 (IOR_144)
G1: J3.15, U6.G1 (IOL_14A_GBIN6)
G2: J3.16, U6.G2 (IOL_14B)
G10: J4.10, U6.G10 (IOR_120)
G11: J4.9, U6.G11 (IOR_129)
GND: C18.1, C19.2, C24.2, C25.1, C26.2, C27.2, J3.1, J3.2, J4.1, J4.2, SW1.1, SW2.1, U5.4 (GND), U6.E5 (GND), U6.E6 (GND), U6.E7 (GND), U6.F5 (GND), U6.F6 (GND), U6.F7 (GND), U6.G5 (GND), U6.G6 (GND), U6.G7 (GND), U6.H5 (GND), U7.5, U7.10, U7.S, X2.2 (GND); also elsewhere on the board
H1: J3.13, U6.H1 (IOL_18A)
H2: J3.14, U6.H2 (IOL_18B)
H10: J4.8, U6.H10 (IOR_116)
H11: J4.7, U6.H11 (IOR_119)
Hsync: U6.J8 (IOB_91), U7.13
J1: J3.11, U6.J1 (IOL_23A)
J2: J3.12, U6.J2 (IOL_25B)
J10: J4.6, U6.J10 (IOR_117)
J11: J4.5, U6.J11 (IOR_114)
K1: J3.9, U6.K1 (IOL_23B)
K2: J3.10, U6.K2 (IOL_25A)
L1: J3.7, U6.L1 (IOB_56)
L2: J3.8, U6.L2 (IOB_61)
MISO: U5.2 (SDO), U6.J9 (IOB_106_SDI); also elsewhere on the board
MOSI: U5.5 (SDI), U6.K9 (IOB_105_SDO); also elsewhere on the board
unnamed: C20.1, C22.1, R13.2, U6.J6 (VCCPLL0)
unnamed: C20.2, C22.2, U6.L6 (GNDPLL0)
unnamed: C21.1, C23.1, R14.2, U6.C6 (VCCPLL1)
unnamed: C21.2, C23.2, U6.C5 (GNDPLL1)
unnamed: R10.1, U5.7 (~HOLD)
unnamed: R11.1, U5.3 (~WP)
unnamed: R17.1, U7.1
unnamed: R18.1, U7.2
unnamed: R19.1, U7.3
unnamed: U6.K6 (IOB_82_GBIN4), X2.3 (OUT)
R: R17.2, U6.D9 (IOR_147)
SCK: U5.6 (SCK), U6.L10 (IOB_107_SCK); also elsewhere on the board
SS: R12.1, U5.1 (~CS), U6.K10 (IOB_108_SS); also elsewhere on the board
Vsync: U6.H9 (IOB_104_CBSEL1), U7.14

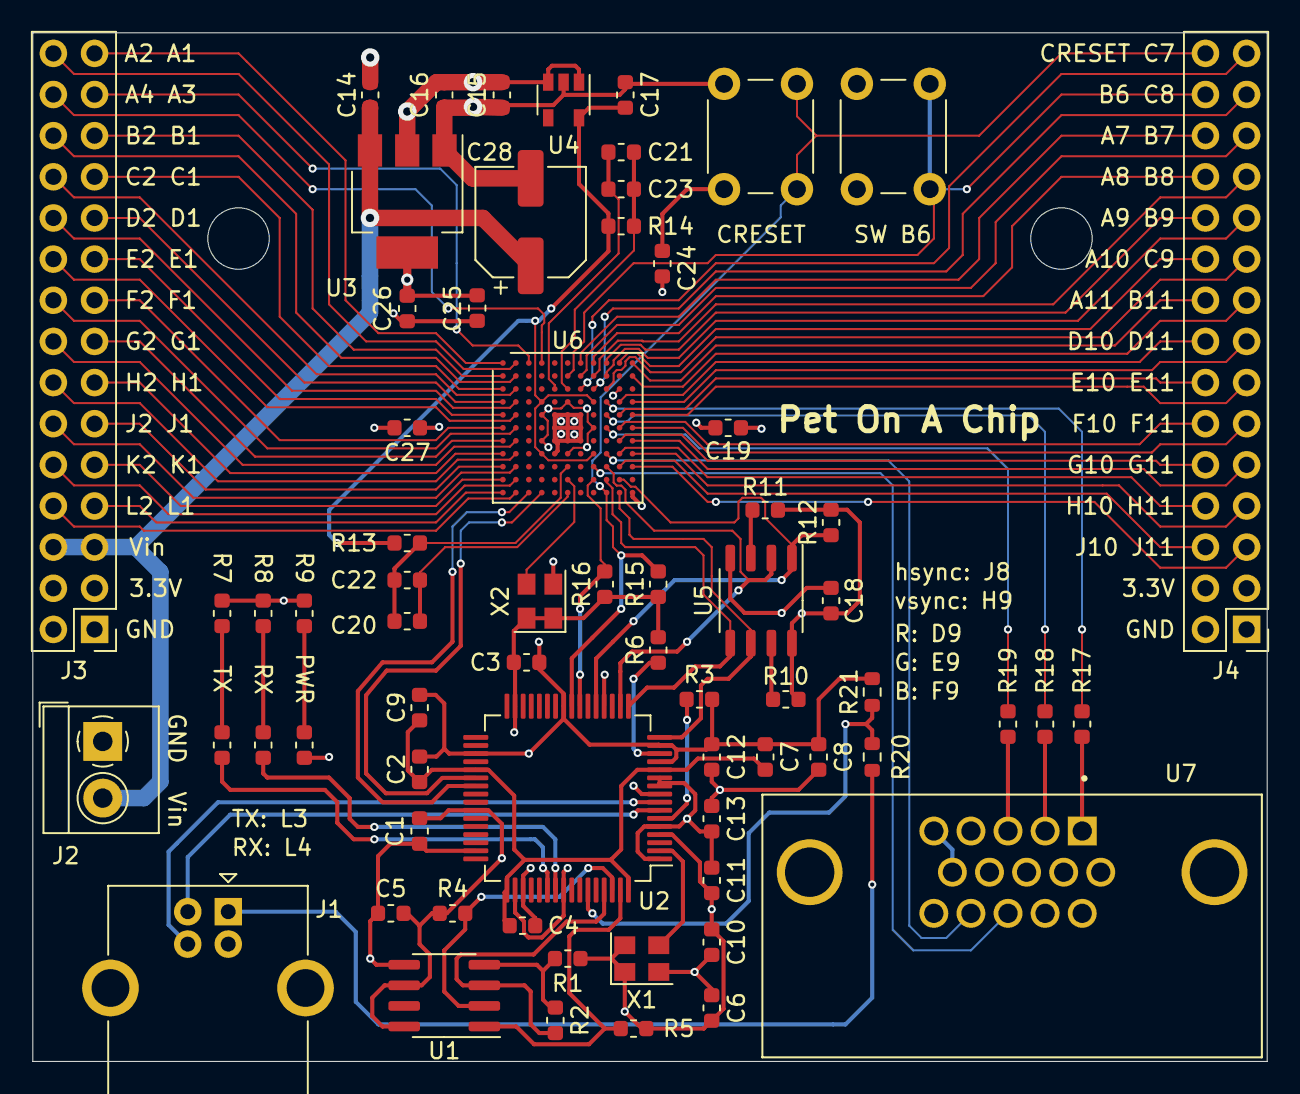
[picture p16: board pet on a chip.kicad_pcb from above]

Board: 4 copper layers, 76.2 x 63.5 mm, 67 parts (0 on the bottom side), 93 nets.

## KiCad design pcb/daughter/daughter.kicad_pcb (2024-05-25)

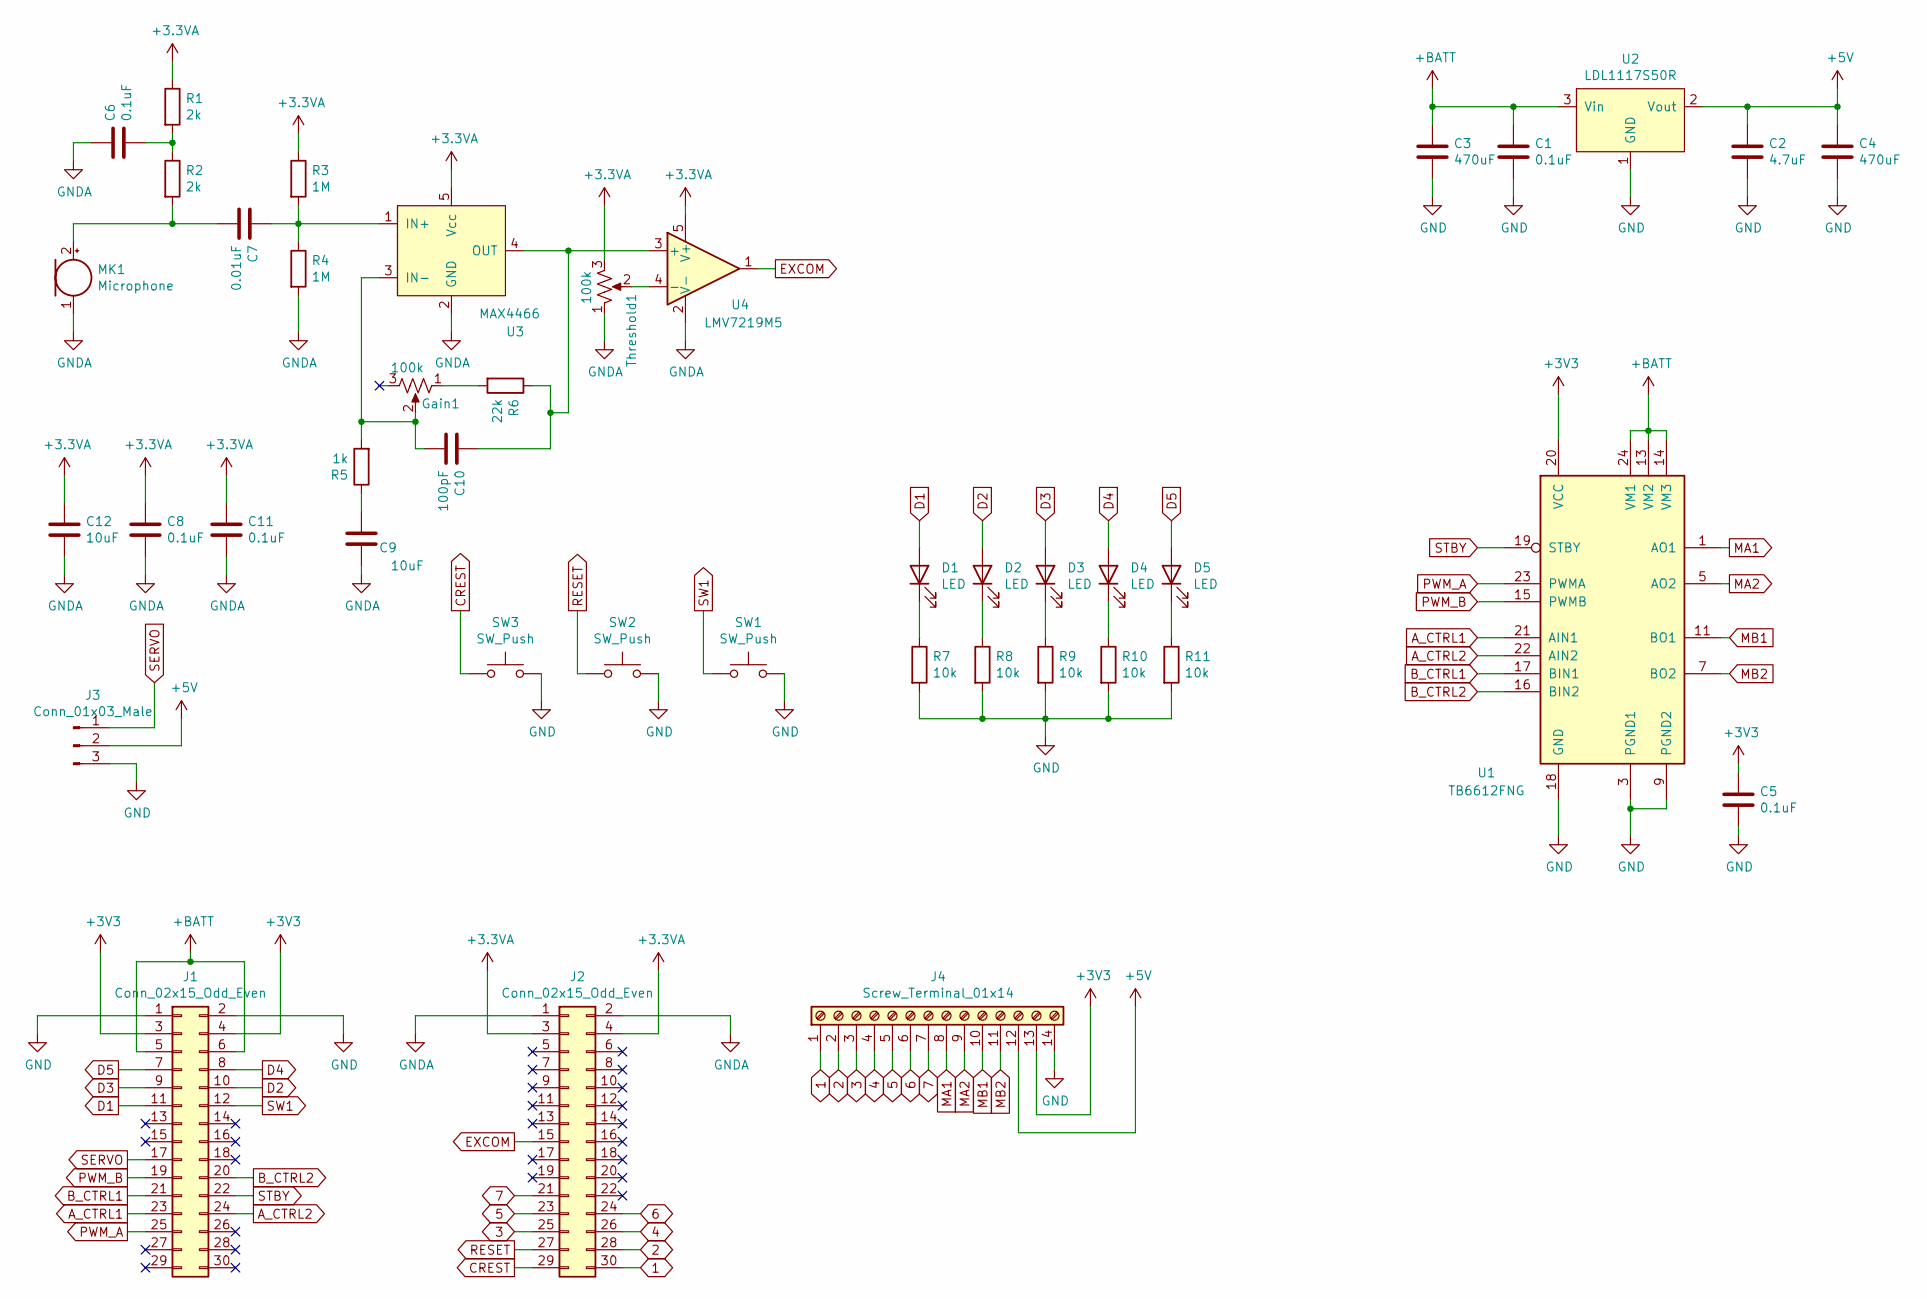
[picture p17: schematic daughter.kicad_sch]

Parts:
C1, C5, C6, C8, C11: 0.1uF; C_0603_1608Metric
C2: 4.7uF; C_0603_1608Metric
C3, C4: 470uF; CP_Elec_6.3x7.7
C7: 0.01uF; C_0603_1608Metric
C9, C12: 10uF; C_0603_1608Metric
C10: 100pF; C_0603_1608Metric
D1, D2, D3, D4, D5: LED; LED_0603_1608Metric
Gain1: 100k; Potentiometer_Bourns_3314J_Vertical
J1, J2: Conn_02x15_Odd_Even; PinHeader_2x15_P2.54mm_Vertical
J3: Conn_01x03_Male; PinHeader_1x03_P2.54mm_Horizontal
J4: Screw_Terminal_01x14; TerminalBlock_4Ucon_1x14_P3.50mm_Horizontal
MK1: Microphone; MIC_CMA-4544PF-W
R1, R2: 2k; R_0603_1608Metric
R3, R4: 1M; R_0603_1608Metric
R5: 1k; R_0603_1608Metric
R6: 22k; R_0603_1608Metric
R7, R8, R9, R10, R11: 10k; R_0603_1608Metric
SW1, SW2, SW3: SW_Push; SW_PUSH_6mm
Threshold1: 100k; Potentiometer_Bourns_3314J_Vertical
U1: TB6612FNG; SSOP-24_5.3x8.2mm_P0.65mm
U2: LDL1117S50R; SOT-223-3_TabPin2
U3: MAX4466; SOT-23-5
U4: LMV7219M5; SOT-23-5

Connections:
1: J2.30, J4.1
2: J2.28, J4.2
3: J2.25, J4.3
4: J2.26, J4.4
5: J2.23, J4.5
6: J2.24, J4.6
7: J2.21, J4.7
+3.3VA: C8.1, C11.1, C12.1, J2.3, J2.4, R1.1, R3.1, Threshold1.3, U3.5 (Vcc), U4.5 (V+)
+3V3: C5.1, J1.3, J1.4, J4.13, U1.20 (VCC)
+5V: C2.1, C4.1, J3.2, J4.12, U2.2 (Vout)
+BATT: C1.1, C3.1, J1.5, J1.6, U1.13 (VM2), U1.14 (VM3), U1.24 (VM1), U2.3 (Vin)
A_CTRL1: J1.23, U1.21 (AIN1)
A_CTRL2: J1.24, U1.22 (AIN2)
B_CTRL1: J1.21, U1.17 (BIN1)
B_CTRL2: J1.20, U1.16 (BIN2)
CREST: J2.29, SW3.1
D1: D1.2 (A), J1.11
D2: D2.2 (A), J1.10
D3: D3.2 (A), J1.9
D4: D4.2 (A), J1.8
D5: D5.2 (A), J1.7
EXCOM: J2.15, U4.1
GND: C1.2, C2.2, C3.2, C4.2, C5.2, J1.1, J1.2, J3.3, J4.14, R7.2, R8.2, R9.2, R10.2, R11.2, SW1.2, SW2.2, SW3.2, U1.3 (PGND1), U1.4 (PGND1), U1.9 (PGND2), U1.10 (PGND2), U1.18 (GND), U2.1 (GND)
GNDA: C6.1, C8.2, C9.1, C11.2, C12.2, J2.1, J2.2, MK1.1 (-), R4.2, Threshold1.1, U3.2 (GND), U4.2 (V-)
MA1: J4.8, U1.1 (AO1), U1.2 (AO1)
MA2: J4.9, U1.5 (AO2), U1.6 (AO2)
MB1: J4.10, U1.11 (BO1), U1.12 (BO1)
MB2: J4.11, U1.7 (BO2), U1.8 (BO2)
unnamed: C6.2, R1.2, R2.1
unnamed: C7.1, R3.2, R4.1, U3.1 (IN+)
unnamed: C7.2, MK1.2 (+), R2.2
unnamed: C9.2, R5.1
unnamed: C10.1, R6.1, U3.4 (OUT), U4.3 (+)
unnamed: C10.2, Gain1.2, R5.2, U3.3 (IN-)
unnamed: D1.1 (K), R7.1
unnamed: D2.1 (K), R8.1
unnamed: D3.1 (K), R9.1
unnamed: D4.1 (K), R10.1
unnamed: D5.1 (K), R11.1
unnamed: Gain1.1, R6.2
unnamed: Threshold1.2, U4.4 (-)
PWM_A: J1.25, U1.23 (PWMA)
PWM_B: J1.19, U1.15 (PWMB)
RESET: J2.27, SW2.1
SERVO: J1.17, J3.1
STBY: J1.22, U1.19 (STBY)
SW1: J1.12, SW1.1

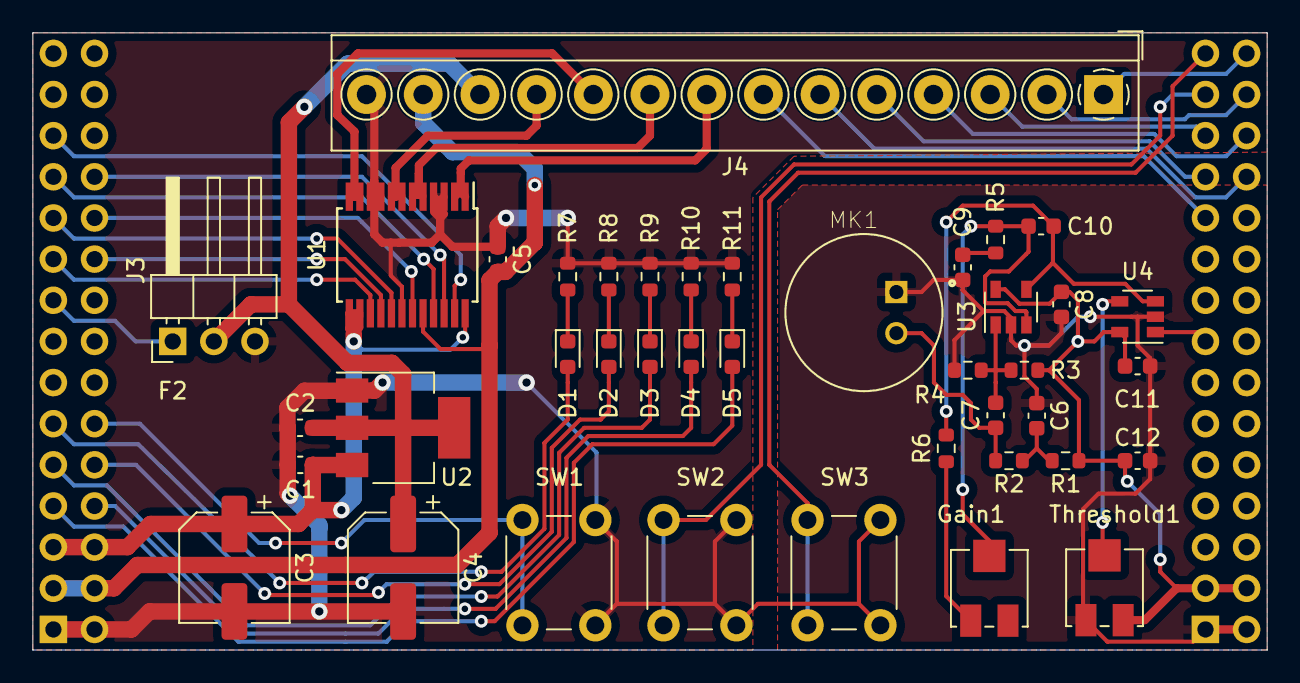
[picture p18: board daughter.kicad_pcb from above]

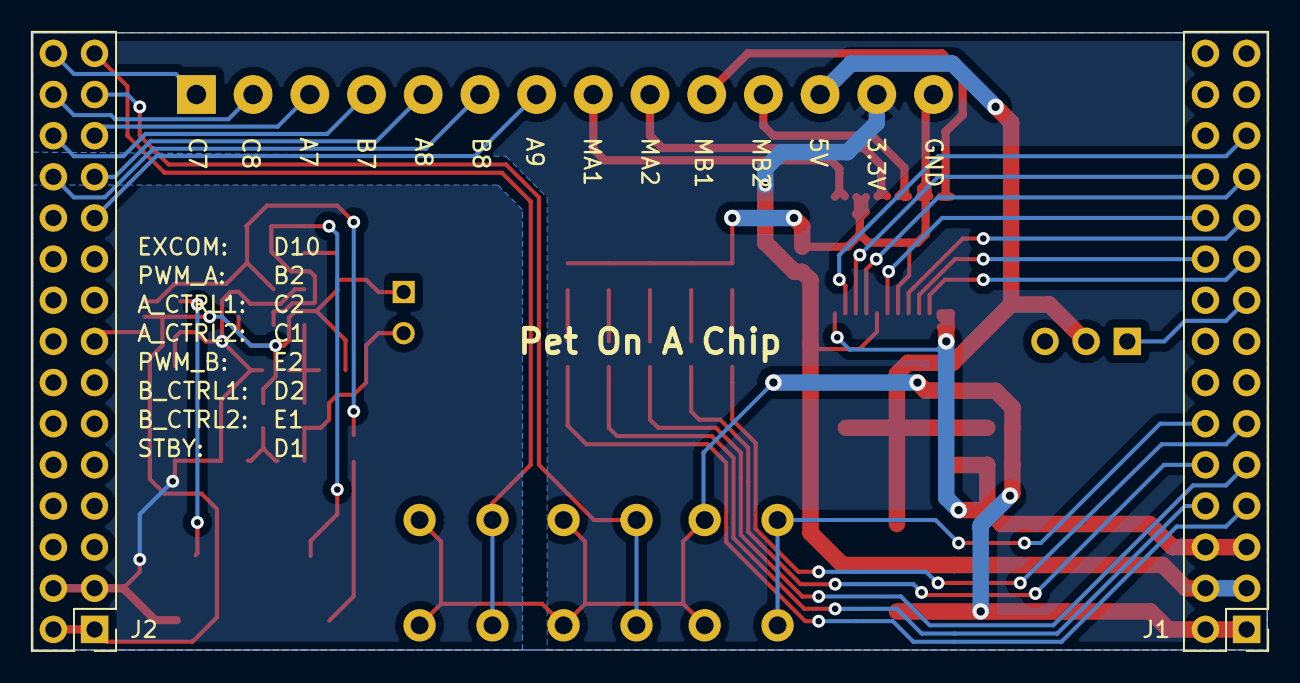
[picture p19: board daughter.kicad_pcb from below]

Board: 2 copper layers, 76.2 x 38.1 mm, 42 parts (2 on the bottom side), 47 nets.

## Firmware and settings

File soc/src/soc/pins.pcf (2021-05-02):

#GPIO
# Note that all gpio pins have pullups enabled.
# See d_ram_and_io.v for details
set_io gpio_pins[0] L2
set_io gpio_pins[1] L1
set_io gpio_pins[2] K2
set_io gpio_pins[3] K1
set_io gpio_pins[4] J2
set_io gpio_pins[5] J1
set_io gpio_pins[6] C7
set_io gpio_pins[7] H11

# UART
set_io rx L4
set_io tx L3

# Motor Controller
set_io pwm[0] B2
set_io pwm[1] E2
set_io motor[0] C2
set_io motor[1] C1
set_io motor[2] D2
set_io motor[3] E1
set_io motor_enable D1
set_io encoders[0] A8
set_io encoders[1] A9

# Servo
set_io servo_pin F2

# Sonar
set_io trig A7
set_io echo C8

# GPU
set_io h_sync J8
set_io v_sync H9
set_io R D9
set_io G E9
set_io B F9

# Reset
set_io -pullup yes reset B6

# Global Clock
set_io clk K6

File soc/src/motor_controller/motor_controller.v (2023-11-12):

module motor_controller(input wire clk,
						input wire [7:0] din,
						input wire [7:0] address,
						input wire w_en,
						input wire r_en,
						output reg [7:0] dout,

						input wire [1:0] encoders,
						output reg [1:0] pwm,
						output reg [3:0] motor,
						output reg enable
);
	parameter F_CPU = 16000000;
	//***************************************************************
	parameter MOTOR_CONTROLLER_ADDRESS = 8'h00;
	localparam MOTOR_ADDRESS = MOTOR_CONTROLLER_ADDRESS;
	localparam ENABLE_ADDRESS = MOTOR_CONTROLLER_ADDRESS + 1;
	localparam SPEED_0_ADDRESS = MOTOR_CONTROLLER_ADDRESS + 2;
	localparam SPEED_1_ADDRESS = MOTOR_CONTROLLER_ADDRESS + 3;
	localparam RPM_0_ADDRESS = MOTOR_CONTROLLER_ADDRESS + 4;
	localparam RPM_1_ADDRESS = MOTOR_CONTROLLER_ADDRESS + 5;
	//***************************************************************
	always @(posedge clk) begin
		case(address)
			MOTOR_ADDRESS: begin
				if(w_en) begin
					motor <= din[3:0];
				end
				if(r_en) begin
					dout <= {4'b0,motor};
				end
			end
			ENABLE_ADDRESS: begin
				if(w_en) begin
					enable <= din[0];
				end
				if(r_en) begin
					dout <= {7'b0,enable};
				end
			end
			SPEED_0_ADDRESS: begin
				if(w_en) begin
					speed_0 <= {1'b0,din[6:0]};
				end
				if(r_en) begin
					dout <= cmpr0;
				end
			end
			SPEED_1_ADDRESS: begin
				if(w_en) begin
					speed_1 <= {1'b0,din[6:0]};
				end
				if(r_en) begin
					dout <= cmpr1;
				end
			end
			RPM_0_ADDRESS: begin
				if(r_en) begin
					dout <= rpm_0;
				end
			end
			RPM_1_ADDRESS: begin
				if(r_en) begin
					dout <= rpm_1;
				end
			end
			default begin
                dout <= 0;
            end
		endcase 
	end
	//***************************************************************
	// PWM
	reg [15:0] prescaler;
	reg scaled;
	localparam SCALE_FACTOR = 16'd125;
	always @(posedge clk) begin
		if(prescaler == SCALE_FACTOR) begin
			scaled <= 1;
			prescaler <= 0;
		end
		else begin
			scaled <= 0;
			prescaler <= prescaler + 1;
		end
	end

	reg [7:0] pwm_counter;
	reg [7:0] cmpr0;
	reg [7:0] cmpr1;
	always @(posedge clk) begin
		if(scaled) begin
			if(pwm_counter == 8'd255) begin         // If finished 256 cycles
                    pwm[0] <= 1;                    // On next edge (start of zero), set the outputs to 1
                    pwm[1] <= 1;
            end
            else begin
                if(pwm_counter == cmpr0) begin     // On match
                	pwm[0] <= 0;                   // clear pwm[0]
                end
                if(pwm_counter == cmpr1) begin     // On match
                	pwm[1] <= 0;                   // clear pwm[1]
                end
            end
            pwm_counter <= pwm_counter + 1;
		end
	end
	//***************************************************************
	// Encoders, RPM Calculation, and Integral Speed Control

	// The encoders have 10 poles, so there are 10 edges per 
	// encoder revolution. The gear ratio is 195.3:1, so there are 
	// 1953 edges per revolution of the wheel. 
	//
	// Our sample window time is 0.1 seconds, so the wheel's RPM can
	// be calulated by:
	// RPM = n*((60*revolution/(1953*encoder_counts))/(0.1 seconds)),
	// where n is the number of encoder counts measured in the 0.1
	// second interval.
	//
	// This reduces to n*(60/195.3) or approximately n*0.3072197.
	// We can write this in binary as n*0.010011101 but this is actually 
	// 0.306640625 in decimal.
	//
	// The quantazation noise is given by 60/195.3 or about 0.3072197 RPM.
	//
	// The maximum speed of the motor is 70 RPM, which corresponds to
	// about n = 227.85. Computing 227.85*(0.3072197 - 0.306640625) gives
	// approximately 0.1319. Thus the rounding gives a maximum error of
	// about 0.1319 RPM.
	//
	// So the maximum error should be about 0.3072 + 0.1319, or
	// 0.4391 RPM. Thus it only makes sense to report the integer portion
	// of the RPM calculation to the user.

	// Synchronizers to prevent metastability and brings the 
	// asynchronous encoder pulses into the clock domain
	reg [1:0] d0 = 0;
	reg [1:0] d1 = 0;
	always @(posedge clk) begin
		d0 <= encoders;
		d1 <= d0;
	end

	// These hold the target RPM values. These are 8-bit signed numbers,
	// but will always be positive. 
	reg [7:0] speed_0 = 0;
	reg [7:0] speed_1 = 0;

	// These hold the number of encoder counts in the 0.1 second window
	reg [7:0] encoder_count_0 = 0;
	reg [7:0] encoder_count_1 = 0;

	// These hold the measured RPM values in fixed point.
	// The upper 7-bits are the integer portion, and the lower
	// 9 bits are the fractional portion
	wire [15:0] full_rpm_0 = encoder_count_0*157;
	wire [15:0] full_rpm_1 = encoder_count_1*157;

	// These hold the measured RPM values, and are updated every 0.1
	// seconds. The MSB is always zero, and the 7 LSBs are from
	// the integer portion of the full_rpm registers. These are
	// 8-bit signed numbers, but will always be positive.
	reg [7:0] rpm_0 = 0;
	reg [7:0] rpm_1 = 0;

	// These hold the difference between the target speed, and
	// the measured RPM. These are 8-bit signed numbers.
	wire [7:0] error_0 = speed_0 - rpm_0;
	wire [7:0] error_1 = speed_1 - rpm_1;

	// These hold the next values of the PWM compare match registers.
	// Checking is done for overflow/underflow in the always block. 
	// These are 9 bit signed numbers.
	wire [8:0] next_0 = {1'b0,cmpr0} + {{1{error_0[7]}},error_0};
	wire [8:0] next_1 = {1'b0,cmpr1} + {{1{error_1[7]}},error_1};

	// Used to detect encoder pulse edges
	reg [1:0] edge_delay = 0;

	always @(posedge clk) begin
		edge_delay <= d1;
		if(strobe) begin
			rpm_0 <= {1'b0,full_rpm_0[15:9]};
			rpm_1 <= {1'b0,full_rpm_1[15:9]};
			encoder_count_0 <= 0;
			encoder_count_1 <= 0;
			if(~next_0[8]) begin
				cmpr0 <= next_0[7:0];
			end
			else begin
				cmpr0 <= {8{~error_0[7]}};
			end
			if(~next_1[8]) begin
				cmpr1 <= next_1[7:0];
			end
			else begin
				cmpr1 <= {8{~error_1[7]}};
			end
		end
		else begin
			if(edge_delay[0] ^ d1[0]) begin
				encoder_count_0 <= encoder_count_0 + 1;
			end
			if(edge_delay[1] ^ d1[1]) begin
				encoder_count_1 <= encoder_count_1 + 1;
			end
		end
	end
	//***************************************************************
	// Sample window generation. Strobe asserts every 0.1 seconds
	// for a single clock cycle
	
	localparam WIDTH = $clog2(F_CPU/10);

	wire [WIDTH:0] strobe_scale_factor = F_CPU/10;

	reg [WIDTH:0] x = 0;
	reg strobe = 0;
	always @(posedge clk) begin
		if(x == strobe_scale_factor) begin
			x <= 0;
			strobe <= 1;
		end
		else begin
			x <= x + 1;
			strobe <= 0;
		end
	end
	//***************************************************************
endmodule

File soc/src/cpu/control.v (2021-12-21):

module control(input wire clk,
               input wire reset,
               input wire [15:0] iMemOut,
               input wire carryFlag,
               input wire zeroFlag,
               input wire negativeFlag,
               input wire interruptEnable,
               output reg regFileSrc,
               output reg [3:0] regFileOutBSelect,
               output reg regFileWriteEnable,
               output wire regFileMove,
               output reg regFileAdd,
               output reg [1:0] regFileConstSrc,            
               output reg aluSrcASelect,
               output reg [1:0] aluSrcBSelect,
               output reg [3:0] aluMode,
               output reg [2:0] dMemDataSelect,
               output reg [1:0] dMemIOAddressSelect,
               output reg dMemIOWriteEn,
               output reg dMemIOReadEn,
               output reg [1:0] statusRegSrcSelect,
               output reg flagEnable,
               output reg [2:0] iMemAddrSelect,
               output reg iMemReadEnable,
               output reg pcWriteEn,
               input wire interrupt,
               output wire intAck,
               output wire reset_out
);    
    //****************************************************************************************************
    // States
    localparam PART1 = 4'b0000;           // Part 1 of instruction (may be single or multi-cycle)
    localparam PART2 = 4'b0010;           // Part 2 of generic multi-cycle instruction
    localparam PART3 = 4'b0100;           // Part 3 of generic multi-cycle instruction

    localparam JMP = 4'b0001;             // Fetch address, and perform a jump
    localparam CALL = 4'b0011;            // Fetch address, and perform a call
    localparam INTERRUPT = 4'b0101;       // Push MSBs of return address, and jump to the ISR
    localparam START = 4'b0111;           // Initial state, wait 40 cycles, and fetch first instruction
    localparam RESET = 4'b1001;           // Reset State

    reg [3:0] state = START;
    reg [3:0] nextState;
    always @(posedge clk) begin
        state <= nextState;
    end
    //****************************************************************************************************
    // Reset Control
    reg reset_d0 = 1;
    reg reset_d1 = 1;
    always @(posedge clk) begin
        reset_d0 <= reset;
        reset_d1 <= reset_d0;
    end

    assign reset_out = (state[3:1] == RESET[3:1] || state[3:1] == START[3:1]);
    //****************************************************************************************************
    // Delayed start counter
    reg [5:0] delay = 0;
    always @(posedge clk) begin
        if(state == START) begin
            delay = delay + 1;
        end
        else begin
            delay <= 0;
        end
    end
    //****************************************************************************************************
    // Logic for jmp, call, and ret conditions
    reg condition;
    always @(*) begin
        case(iMemOut[15:13])
        3'b000:    condition = 1'b1;
        3'b001:    condition = (carryFlag);
        3'b010:    condition = (~carryFlag);
        3'b011:    condition = (zeroFlag);
        3'b100:    condition = (~zeroFlag);
        3'b101:    condition = (negativeFlag);
        3'b110:    condition = (~negativeFlag);
        3'b111:    condition = 1'b1;
        endcase 
    end
    //****************************************************************************************************
    // Interrupt control
    assign intAck = (state == INTERRUPT);
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

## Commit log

2021-04-14 added gerbers
    [delux pet on a chip-B_Cu.gbr, delux pet on a chip-B_Mask.gbr, delux pet on a chip-B_Paste.gbr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]
2021-04-14 fixed 3d model paths
    [Daughter.kicad_pcb, cma-4544pf-w.stp, delux pet on a chip.kicad_pcb]
2021-04-24 switched from subtract with borrow to subtract with carry. fixed bug in control for pus and pos.
    [control.v, divide.asm]
2021-04-25 fixed bugs in shell
    [shell.asm]
2021-04-26 updated shell program and modified uart_io.asm for safty
2021-04-26 assembler can now produce strings without null termination. shell program working.
2021-06-20 fixed concatenation syntax in motor controller
    [motor_controller.v]
2021-07-02 cleaned up assembler source
2021-10-08 cleaned up assembler.py
2021-10-21 fixed bugs in assembler
2021-12-20 working on interrupt controller
2021-12-21 fixed memory map error
    [pic.v]
2021-12-21 fixed bugs in counter_timer.v
    [counter_timer.v, pic.v]
2021-12-21 fixed bug in counter.asm
    [counter.asm]
2022-01-02 Moved from KiCad 5 to KiCad 6, and fixed bad organization
    [Daughter.kicad_pcb, Daughter.sch, FPGA.kicad_sch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]
2022-01-02 cleaned up pcb stuff
2022-01-02 cleaned up kicad stuff
    [ASTX-H11.STEP, ASTX-H12.STEP, D8.stp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]
2022-01-03 cleaned up pcb location
    [pet on a chip.kicad_pcb]
2022-01-28 updated servo comments and adjusted for new servo
2022-01-28 fixed servo math
2022-08-02 fixed up assembler
2023-02-07 Update pic.v
    fixed addressing issue
    [pic.v]
2023-03-16 updated to KiCad 7
    [daughter.kicad_pcb, daughter.kicad_sch, fpga.kicad_sch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]
2023-04-24 fixed issues with shell
    [shell.asm]
2023-04-25 updated sonar rtl. something is up with the first reading. I don't think it is the rtl. My guess is that the module might have to be pinged once to settle. not sure however.
2023-06-24 parameterizing servo
2023-06-24 added note to uart.v
2023-11-12 fixed serious flaw with parameterization of motor controller
    [avoid2.asm, blink.asm, motor_controller.v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]
2024-05-25 updated to kicad 8
    [daughter.kicad_pcb, daughter.kicad_sch, fpga.kicad_sch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]
